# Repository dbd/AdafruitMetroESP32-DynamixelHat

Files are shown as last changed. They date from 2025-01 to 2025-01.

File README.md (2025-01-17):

# AdafruitMetroESP32-DynamixelHat

A HAT designed for the [AdaFruit Metro ESP32-S3](https://learn.adafruit.com/adafruit-metro-esp32-s3) to communicate with Dynamixel servos using this [library](https://github.com/dbd/CircuitPythonDynamixel)



# Bill of Materials
| Item | Link | Quantity | Unit Cost | Item Cost |
| ---- | ---- | --- | --- | --- |
| TXB0104PWR Level Shifter | [Link](https://www.digikey.com/short/qm0td78w) | 1 | $0.87 | $0.87 | 
| SN74LVC2G241DCTR Tri-state buffer | [Link](https://www.digikey.com/short/1w0w74jb) | 1 | $0.40 | $0.40 | 
| 10k Resistor | [Link](https://www.digikey.com/short/27n7pcz3) | 4 | $0.10 | $0.40 | 
| 0.1 µF Capacitor | [Link](https://www.digikey.com/short/hjtz927q) | 6 | $0.10 | $0.60 | 
| 100 µF Capacitor | [Link](https://www.digikey.com/short/43pqprtd) | 1 | $1.73 | $1.73 | 
| JST Header | [Link](https://www.digikey.com/short/h1hjcqr2) | 3 | $0.46 | $1.38 | 
| 8P Header | [Link](https://www.digikey.com/short/35q99nnb) | 2 | $1.42 | $2.84 | 
| 6P Header | [Link](https://www.digikey.com/short/1hd3z8d7) | 1 | $1.80 | $1.80 | 
| 10P Header | [Link](https://www.digikey.com/short/rm5nhzqt) | 1 | $2.19 | $2.19 | 
| PCB Fab | | 5 | 2 | ~$20 |
| | | | Total Cost | $32.21|

# Assembly
Hand soldering this is not for the faint of heart. If you don't own a hotplate and solder paste I would recommend having your PCB fab doing all the SMD component assembly and then purchasing the 100 µF capacitor and headers to solder yourself. 
Otherwise all components are labeled and assuming your PCB has silk screen printing, it should just be matching footprints. 
A "cheap" hotplate can be found for ~$55 on Amazon and should be sufficient with some cheap solder paste in a syringe to go along.

If the JST connectors don't match the footprint, try inserting them the otherway. Incorrectly soldering them shouldn't cause harm since the 12v line is in the middele regardless but I don't recommend finding out.

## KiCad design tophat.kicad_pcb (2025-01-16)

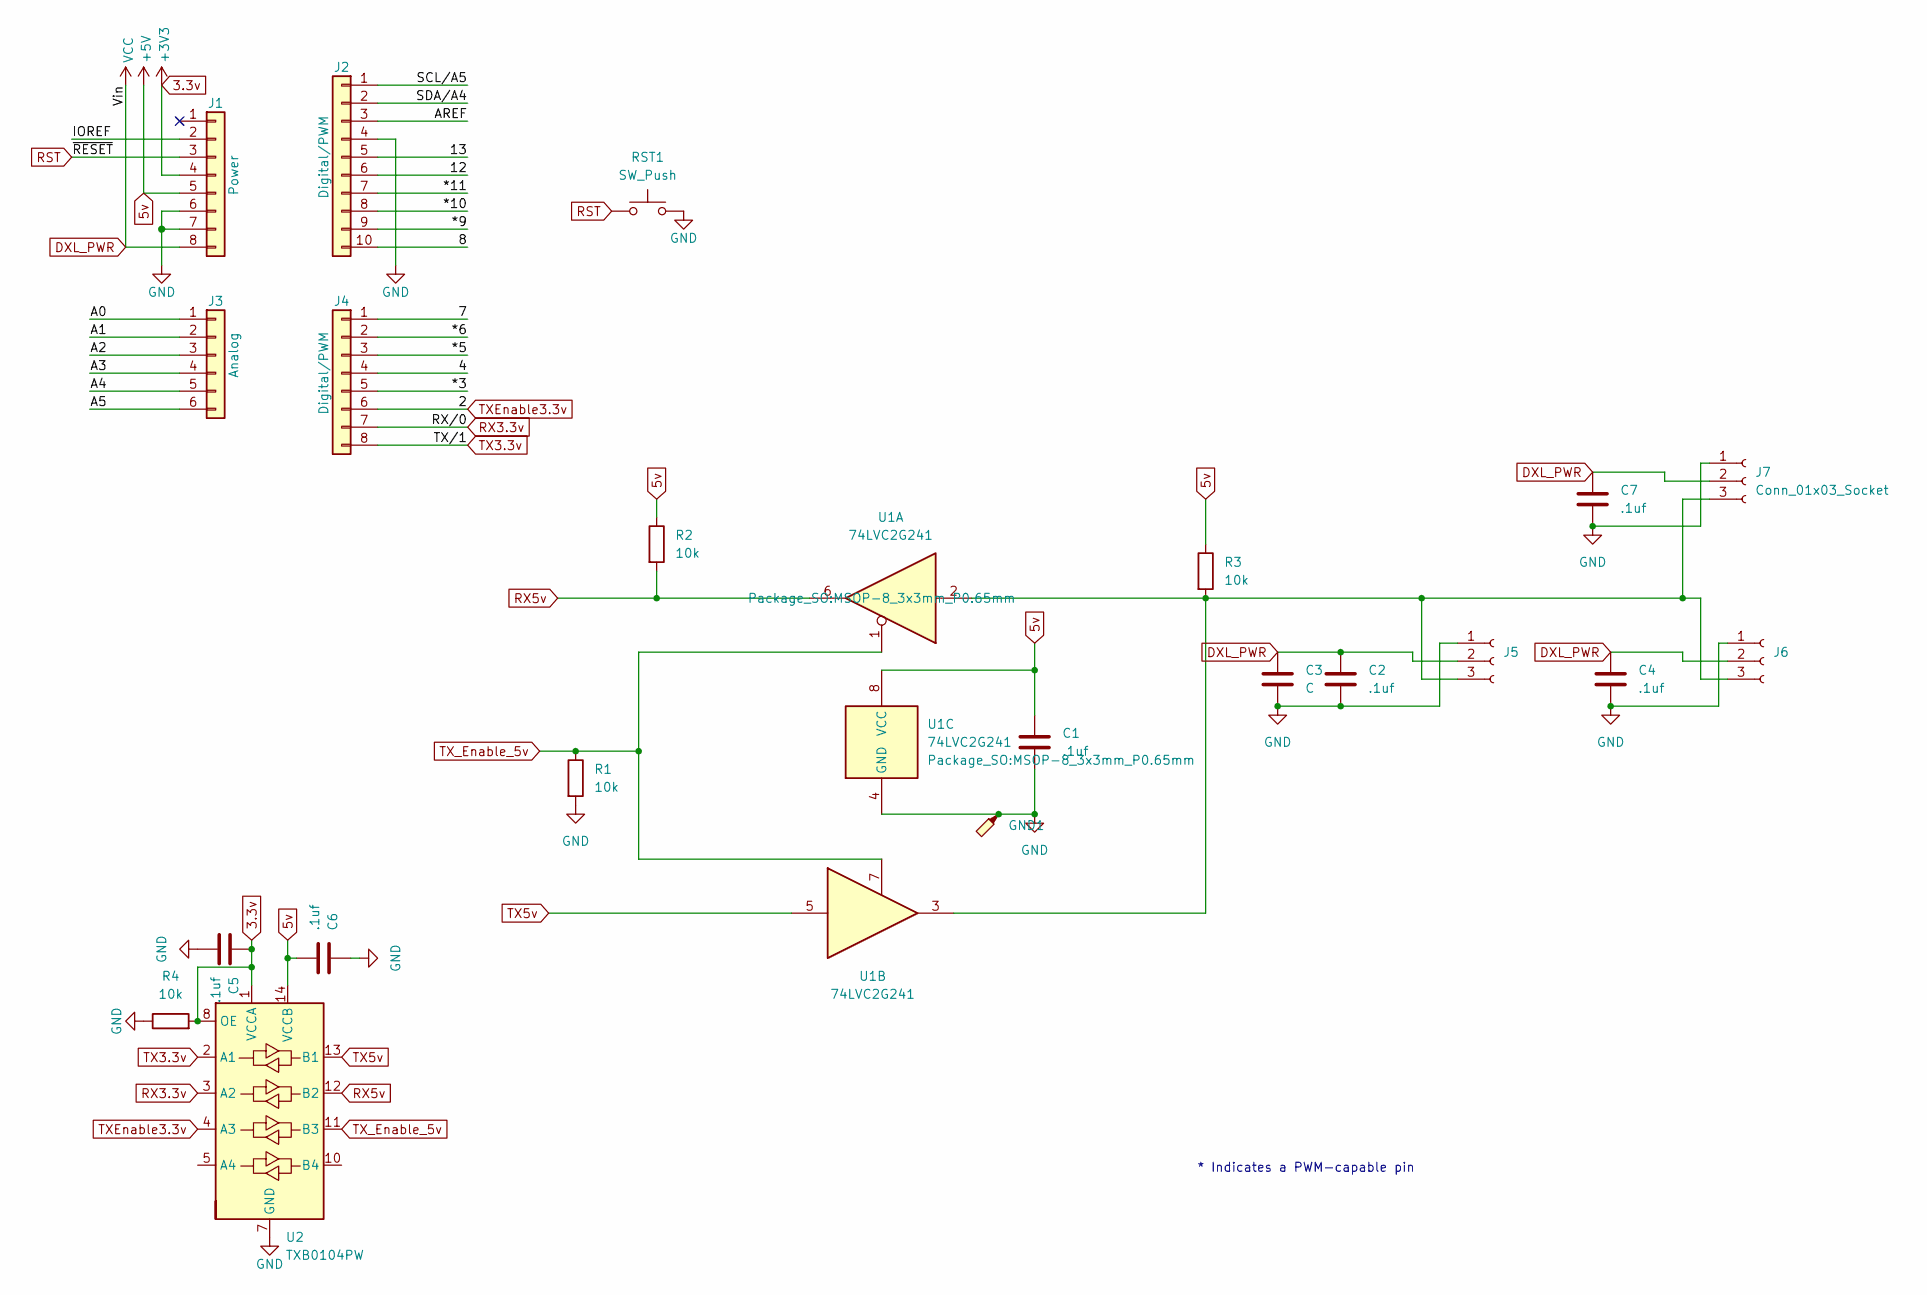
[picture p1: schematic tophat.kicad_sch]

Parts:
C1, C2, C4, C5, C6, C7: .1uf; 0805
C3: C; CP_Elec_8x6.2
GND1: TestPoint_Probe; TestPoint_Pad_1.0x1.0mm
J1: Power; PinSocket_1x08_P2.54mm_Vertical
J2: Digital/PWM; PinSocket_1x10_P2.54mm_Vertical
J3: Analog; PinSocket_1x06_P2.54mm_Vertical
J4: Digital/PWM; PinSocket_1x08_P2.54mm_Vertical
J5, J6, J7: Conn_01x03_Socket; JST_EH_B3B-EH-A_1x03_P2.50mm_Vertical
R1, R2, R3, R4: 10k; 0805
RST1: SW_Push; SW_Tactile_SPST_NO_Straight_CK_PTS636Sx25SMTRLFS
U1: 74LVC2G241; MSOP-8_3x3mm_P0.65mm
U2: TXB0104PW; TSSOP-14_4.4x5mm_P0.65mm

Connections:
3.3v: C5.1, J1.4, R4.2, U2.1 (VCCA), U2.8 (OE)
5v: C1.1, C6.2, J1.5, R2.1, R3.1, U1.8 (VCC), U2.14 (VCCB)
/4: J4.4
/7: J4.1
/8: J2.10
/12: J2.6
/13: J2.5
/*3: J4.5
/*5: J4.3
/*6: J4.2
/*9: J2.9
/*10: J2.8
/*11: J2.7
/A0: J3.1
/A1: J3.2
/A2: J3.3
/A3: J3.4
/A4: J3.5
/A5: J3.6
/AREF: J2.3
/IOREF: J1.2
/SCL/A5: J2.1
/SDA/A4: J2.2
DXL_PWR: C2.1, C3.1, C4.1, C7.1, J1.8, J5.2, J6.2, J7.2
GND: C1.2, C2.2, C3.2, C4.2, C5.2, C6.1, C7.2, GND1.1, J1.6, J1.7, J2.4, J5.1, J6.1, J7.1, R1.2, R4.1, RST1.2, U1.4 (GND), U2.7 (GND)
unnamed: J5.3, J6.3, J7.3, R3.2, U1.2, U1.3
RST: J1.3, RST1.1
RX3.3v: J4.7, U2.3 (A2)
RX5v: R2.2, U1.6, U2.12 (B2)
TX3.3v: J4.8, U2.2 (A1)
TX5v: U1.5, U2.13 (B1)
TXEnable3.3v: J4.6, U2.4 (A3)
TX_Enable_5v: R1.1, U1.1, U1.7, U2.11 (B3)

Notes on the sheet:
* Indicates a PWM-capable pin

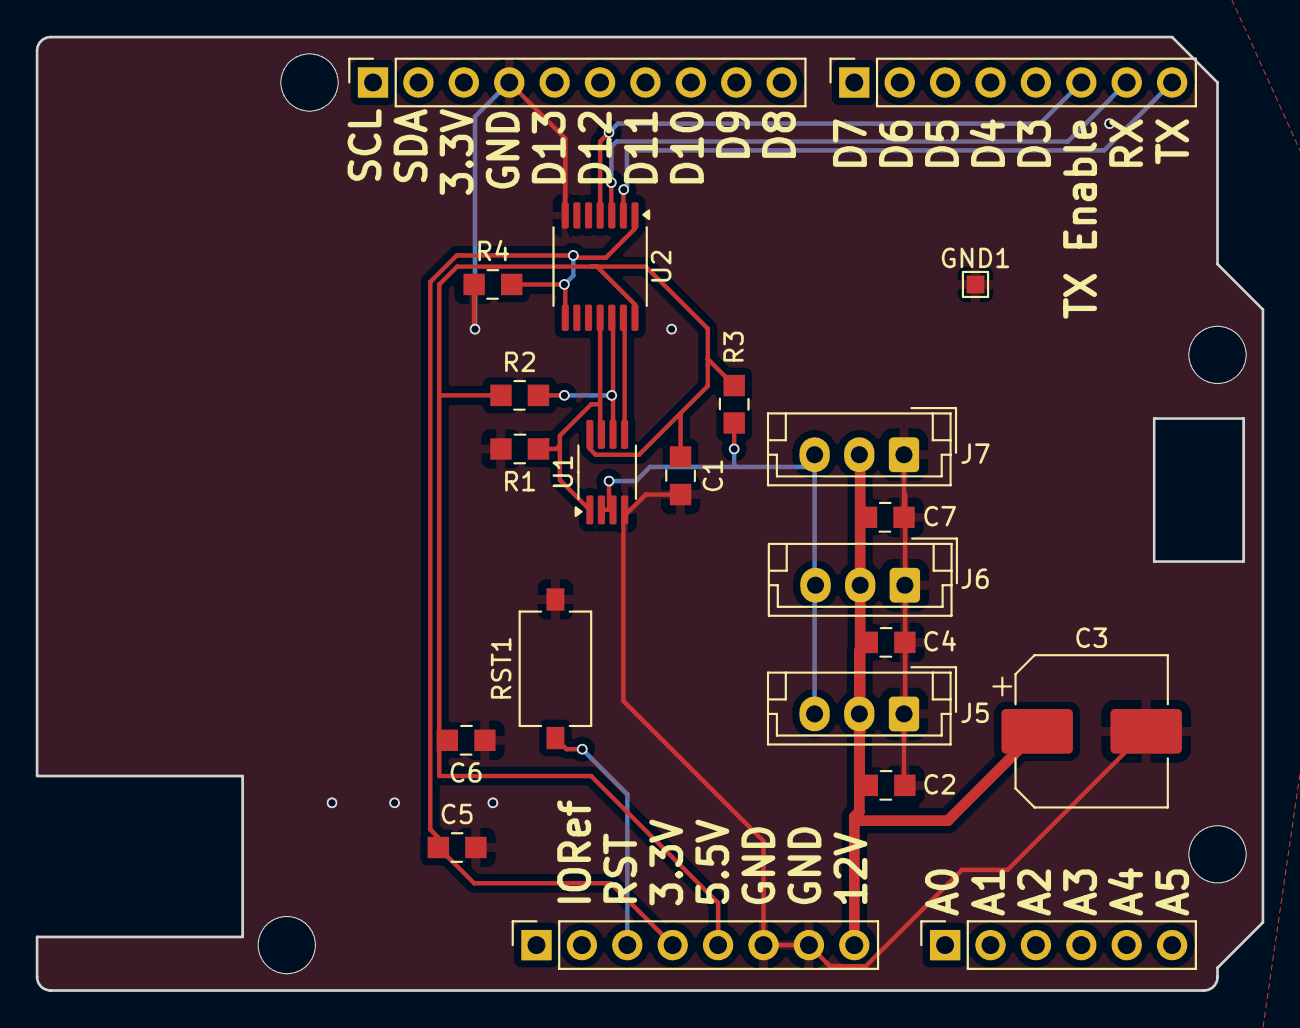
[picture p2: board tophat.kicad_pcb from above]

Board: 2 copper layers, 68.6 x 53.3 mm, 26 parts (0 on the bottom side), 12 nets.

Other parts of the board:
MH1, MH2, MH3, MH4: MountingHole_3.2mm

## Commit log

2025-01-16 Add BOM
2025-01-16 Add silk screen and fix up schematic
    [tophat-B_Cu.gbl, tophat-B_Mask.gbs, tophat-B_Paste.gbp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]
